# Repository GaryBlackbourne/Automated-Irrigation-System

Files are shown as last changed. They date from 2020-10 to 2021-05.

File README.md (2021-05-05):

# Automated-Irrigation-System

This project is the successor of the watering-system project, which is to be discontinued.

The first prototype of the node unit is released, and ready to be used.

## Current state:
  - Hardware documentation completed
  - Board schematic and layout are in final state
  - board is ready (one prototype finished and tested)

  - node unit source code is ready, and tested
  - manual requests can be made by <node_ip>/measure

## Usage:
  - clone the project
  - install esp-idf framework, and create a project (details in doc/dev-diary.md)
  - insert source files into `main` directory
  - change the SSID and passphrase in `credentials.h`
  - build and flash the project

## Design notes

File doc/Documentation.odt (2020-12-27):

Automated Irrigation System Documentation

Head unit board v 0.1

The Automated Irrigation system is a fully automated modular system for smart home gardening. A central control unit controls multiple head units, that measure the plants condition, and based on the instructions given by the main control, irrigate the plant as needed.

This documentation contains information ONLY abut the alpha version of the head units board.

Board Features:

1. Measure soil moisture
2. Measure temperature
3. Measure light
4. Drive Irrigation pump

Realization:

- Moisture: 555 timer RC capacity measure
- Temperature: in box measurement
- Light: in box measurement
- Watering pump: common source motor drive circuit

Controller: EFM32GG Giant Gecko Starter Kit

PCB editor: KiCAD

Basic Head unit functionality:

The microcontroller drives the sensors, reads temperature, moisture and light data. Based on measured data, the controller drives an external pump, to irrigate the plants’ soil. The connection between the controller and the board is estabilished through the pin array.

Temperature sensor:

The used IC for temperature measurement is an LM75C. The chip uses I2C bus to communicate with the controller, therefore connected to the on board I2C bus. (This bus is shared with VEML7700)

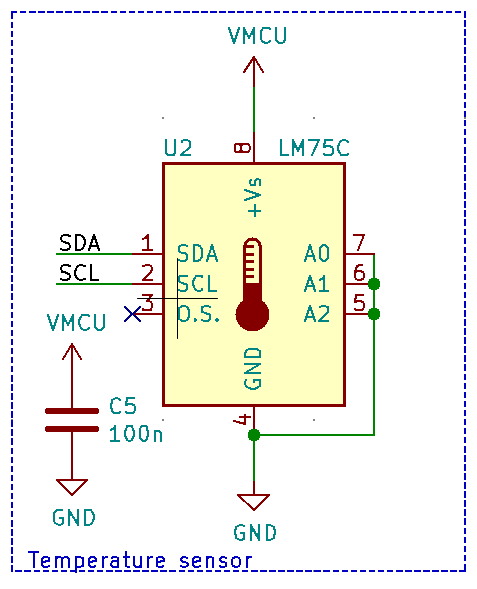
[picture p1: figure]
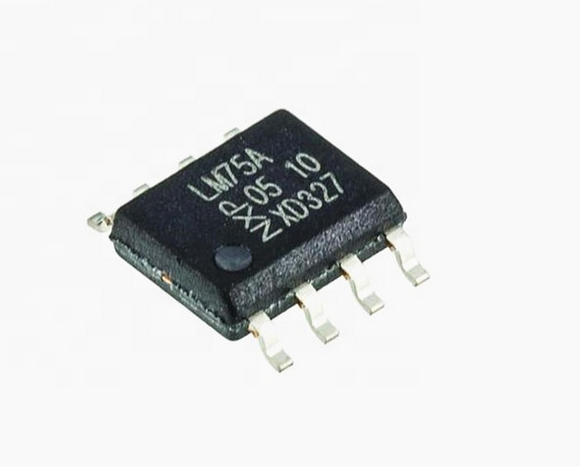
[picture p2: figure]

Moisture sensor:

Moisture measurement method is based on capacity measurement. The measurement is based on a TLC555 timer IC in astable mode. The measured capacity controls the frequency of the timer, which is connected to the PD0 pin on the microcontroller. This pin can be configured as an external clock for pulse counter unit. This method is easier to implement in software, because the capacity measurement becomes a single counting problem.

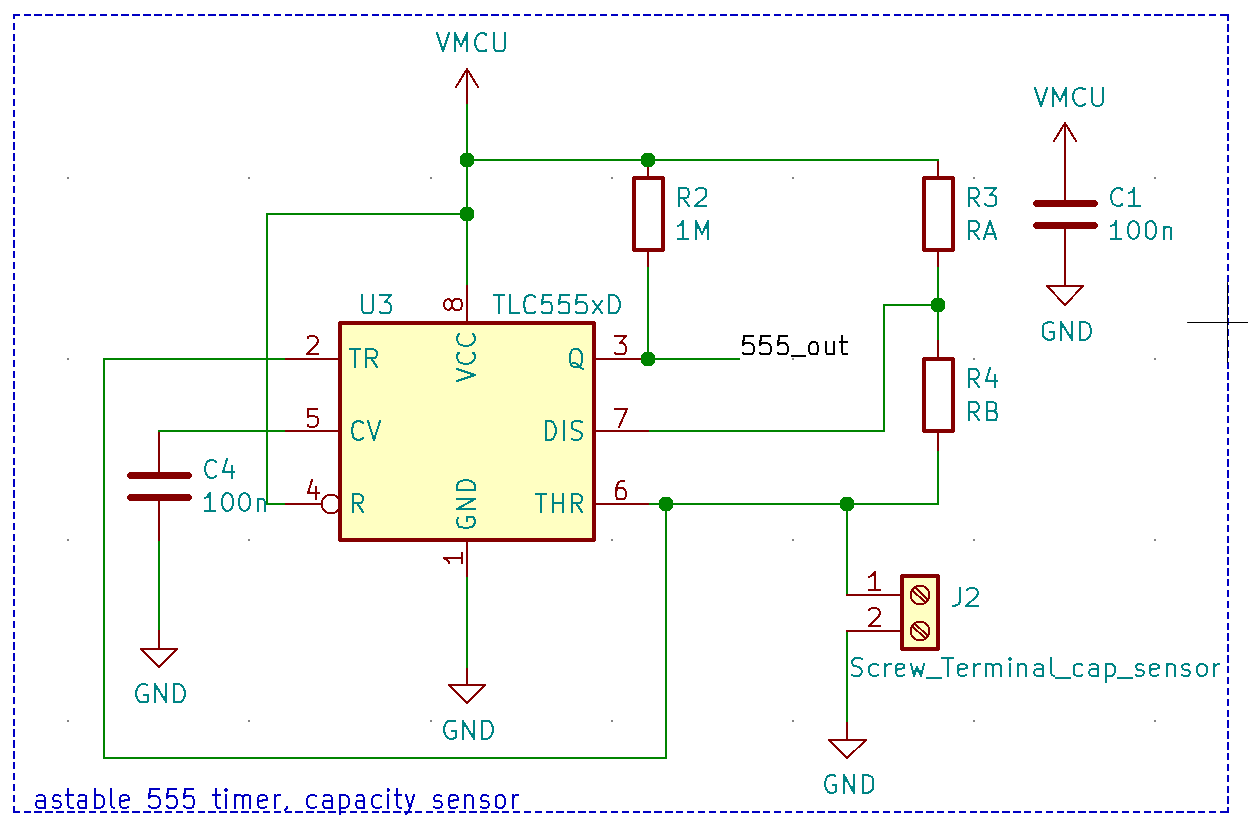
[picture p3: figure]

RA and RB are to be measured with the probe capacity in mind.

Light sensor:

Light measurement is done via VEML7700 IC. This chip is communicating with the microcontroller on I2C protocol, therefore connected to the I2C bus on the board. This component is easy to connect, because the power voltage is 3.3V, no conversion needed. The bus is shared with the temperature sensor.

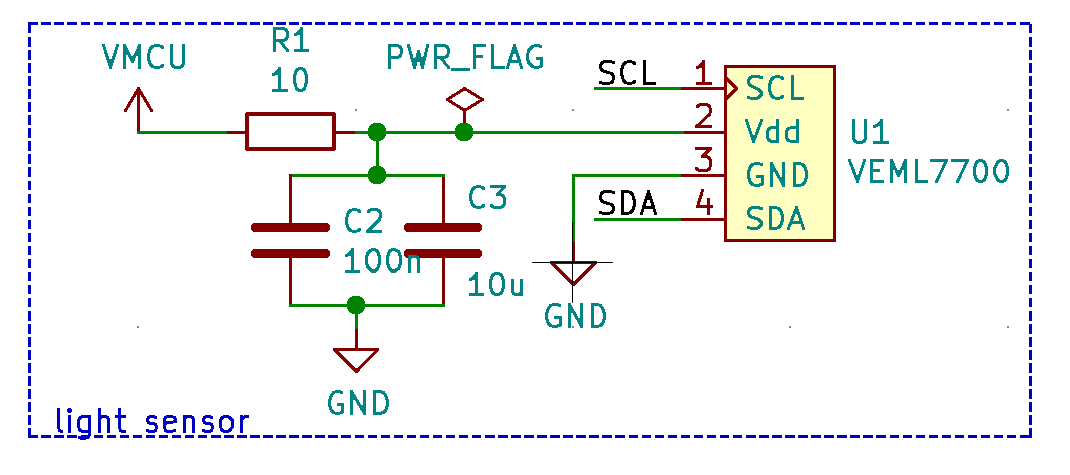
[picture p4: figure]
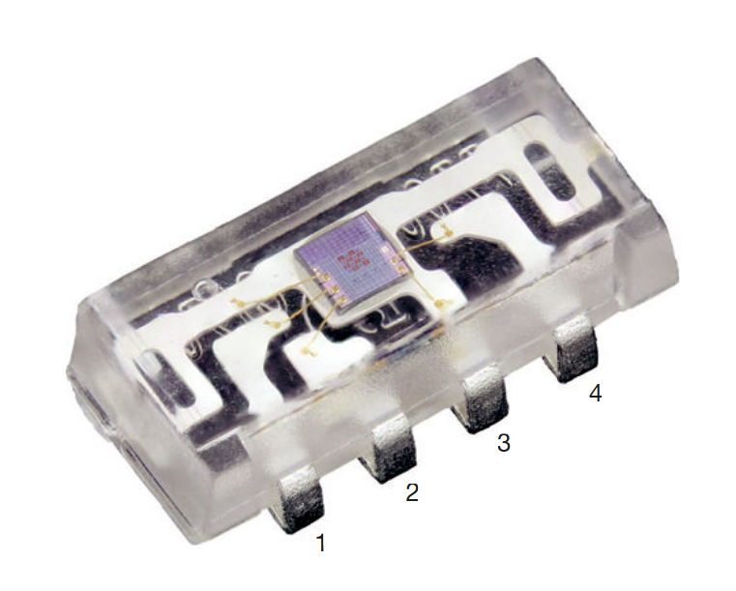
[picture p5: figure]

Package:

Project is packaged in an IP67 plastic case. The case has to protect the device from water, and dust, that may be common at the area of application and may damage the unprotected board. Without casing, only indoor use is possible.

-Pump:

The control element of the system is one 12V pump, a Barwig 0333. The pump requires a 12V power supply that must be connected to the board externally. To maintain the water stream, this pump needs 1.5A–2A current, which makes it necessary to drive with a transistor. The chosen IRLML2502 transistor is a logic level FET. The gate can be driven with a GPIO, and the Drain-Source current allows the required current for the motor.

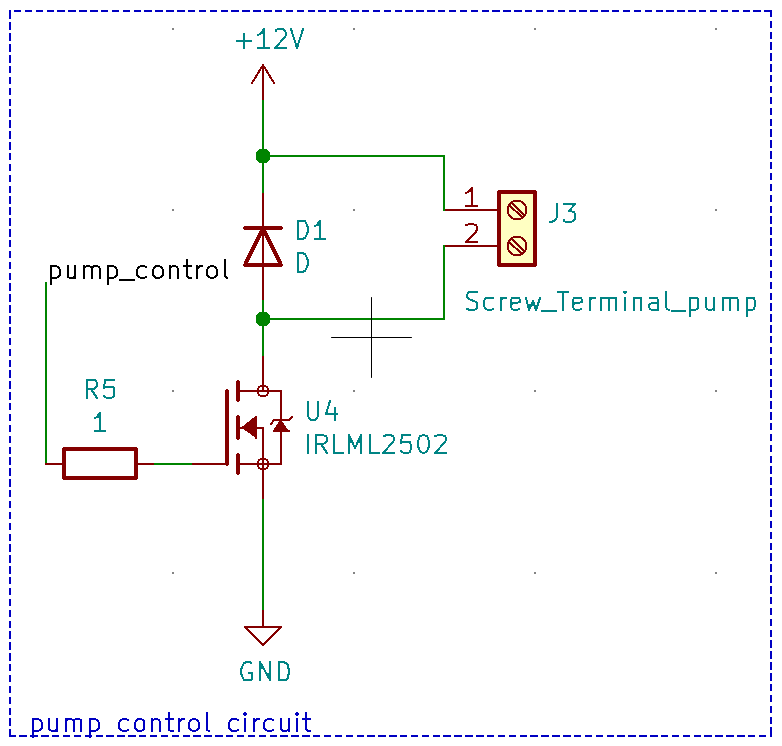
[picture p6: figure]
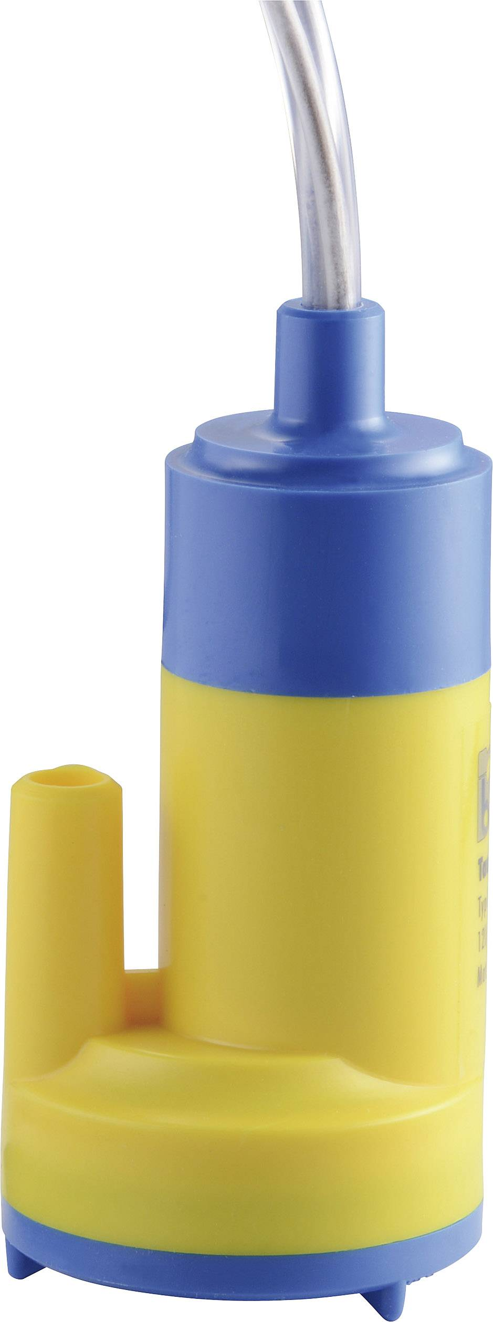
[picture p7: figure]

The pump is driven by a simple common source circuit.

-Power Supply:

The device is powered with an LPV-35-12 power supply unit, which provides 12V DC for the pump.

Alternatively, a barrel jack input is supported if 12V DC input is available. When the barrel jack is in use the LPV power supply is out of use.

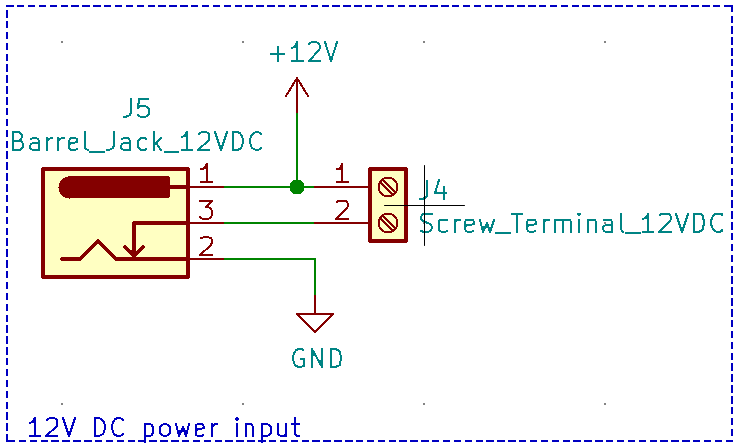
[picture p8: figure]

-Connectors:

The board has five connectors.

1. Pin array to connect to the giant gecko controller. (2x10 pin array female)
2. screw terminal for capacity measure device
3. screw terminal for pump drive
4. screw terminal for 12V DC input
5. barrel jack, for 12V DC input

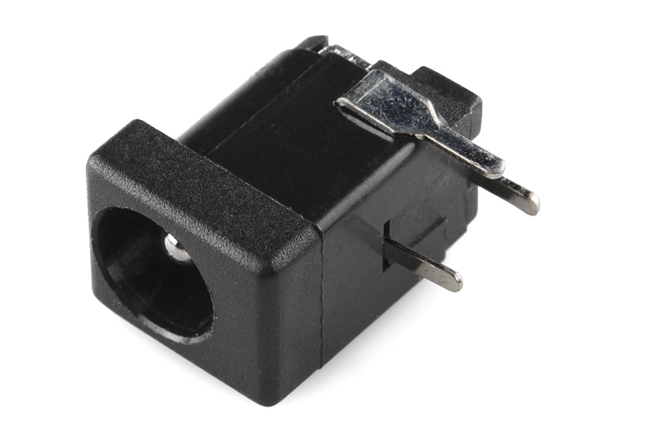
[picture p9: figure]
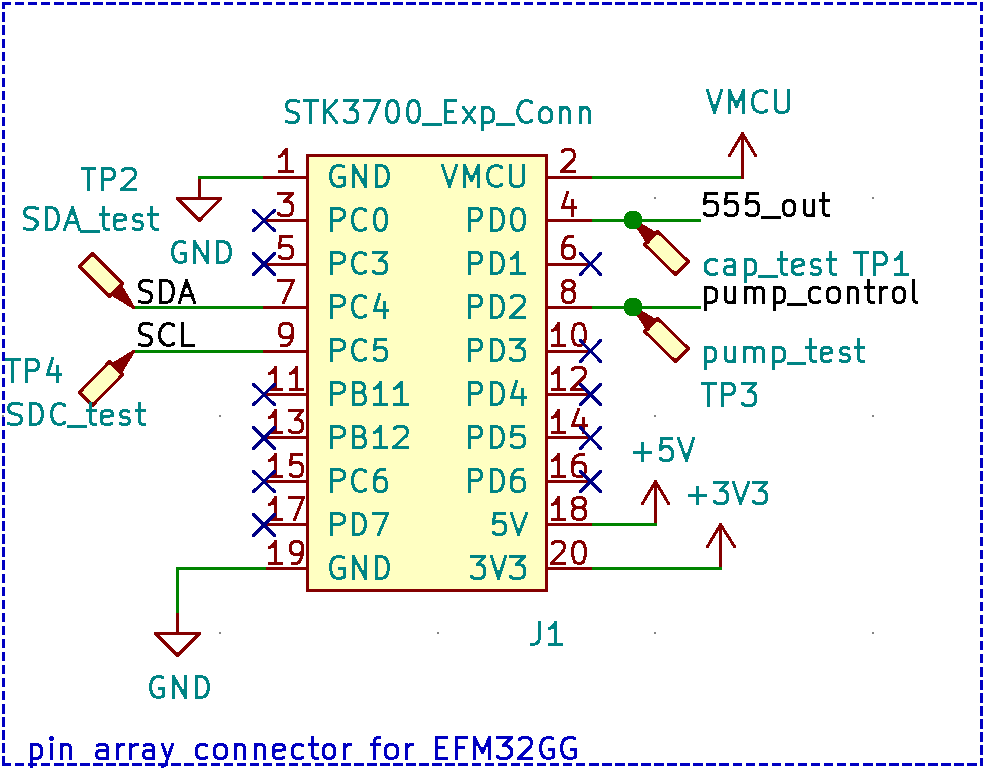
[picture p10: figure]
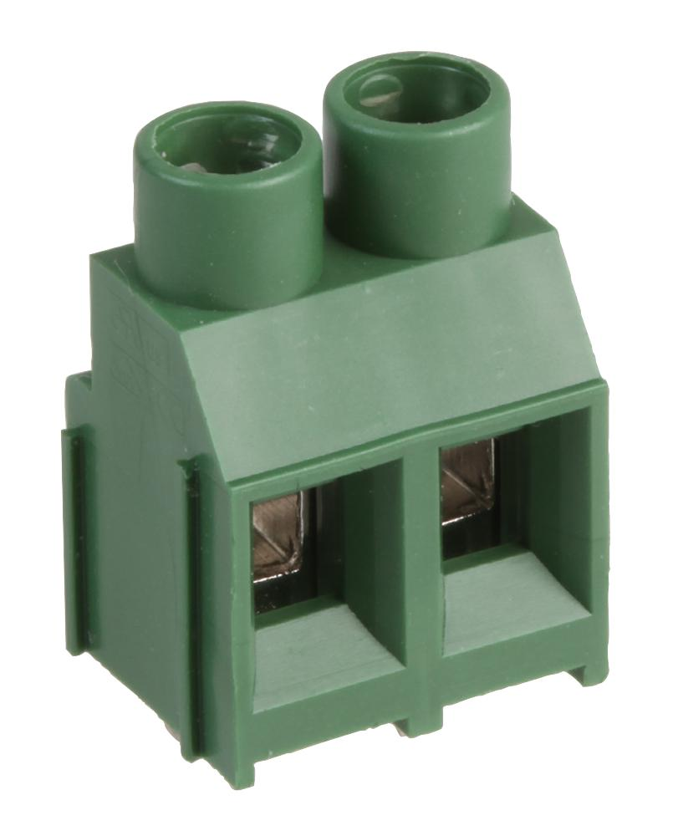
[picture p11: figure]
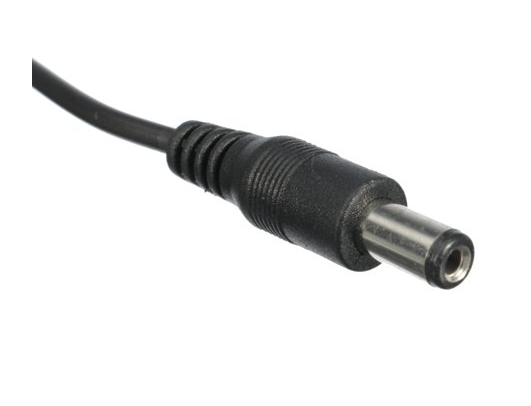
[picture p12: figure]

-Schematic:

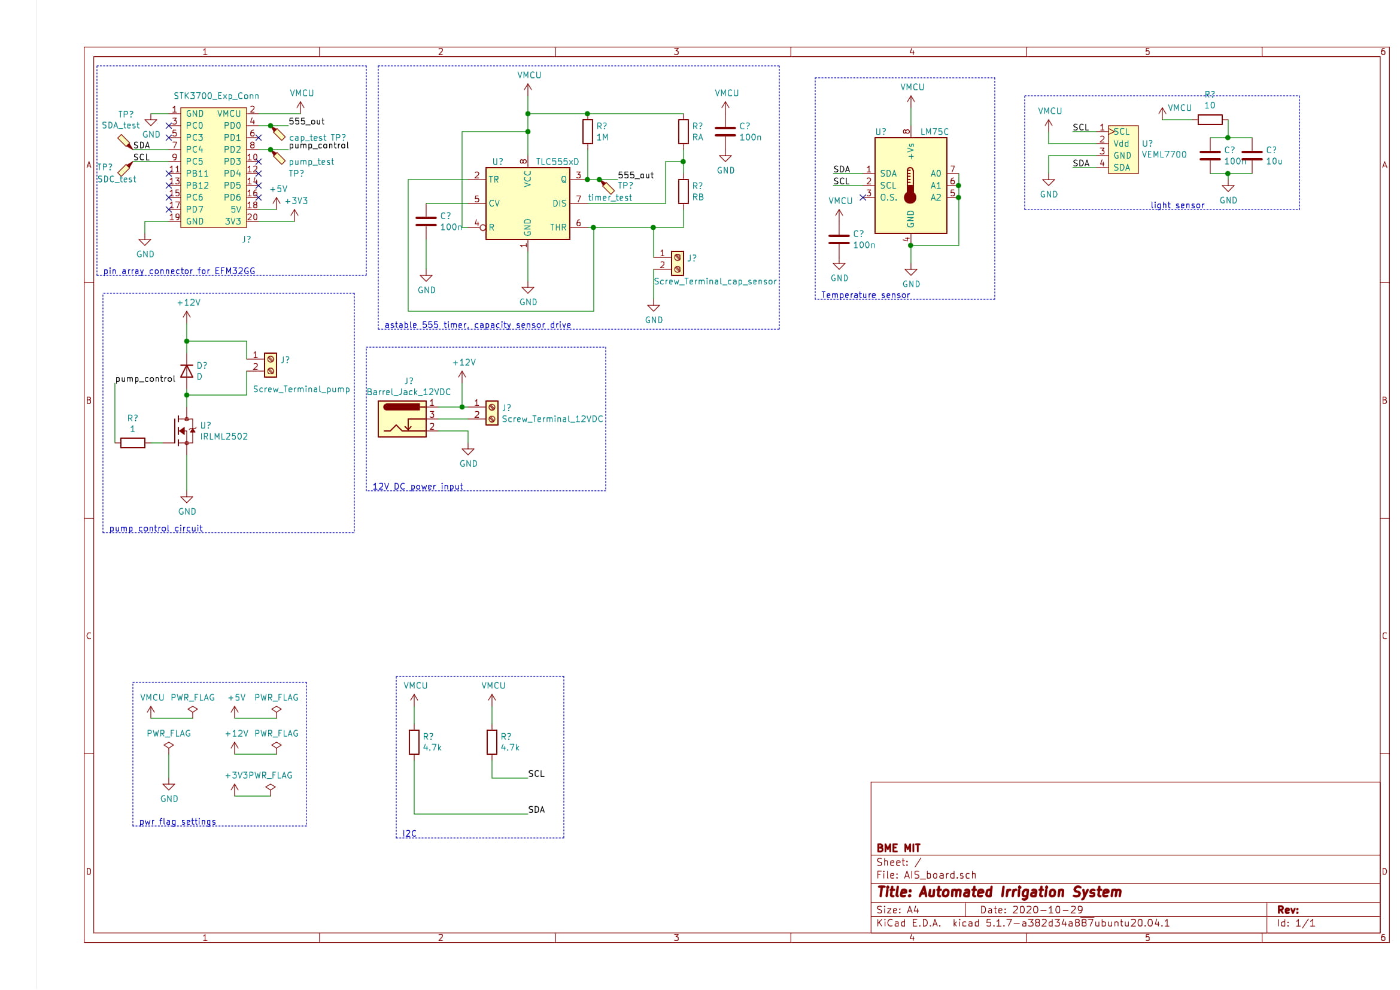
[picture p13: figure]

-PCB layout:

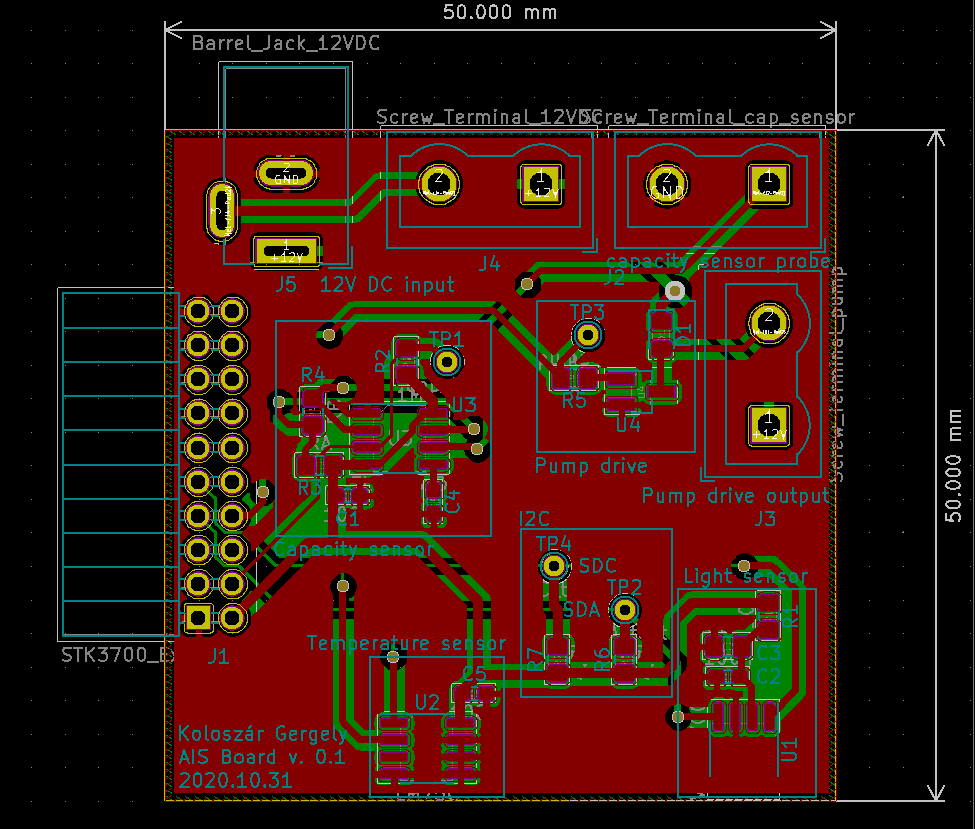
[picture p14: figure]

-Prototype Hardware (kiCAD 3D model):

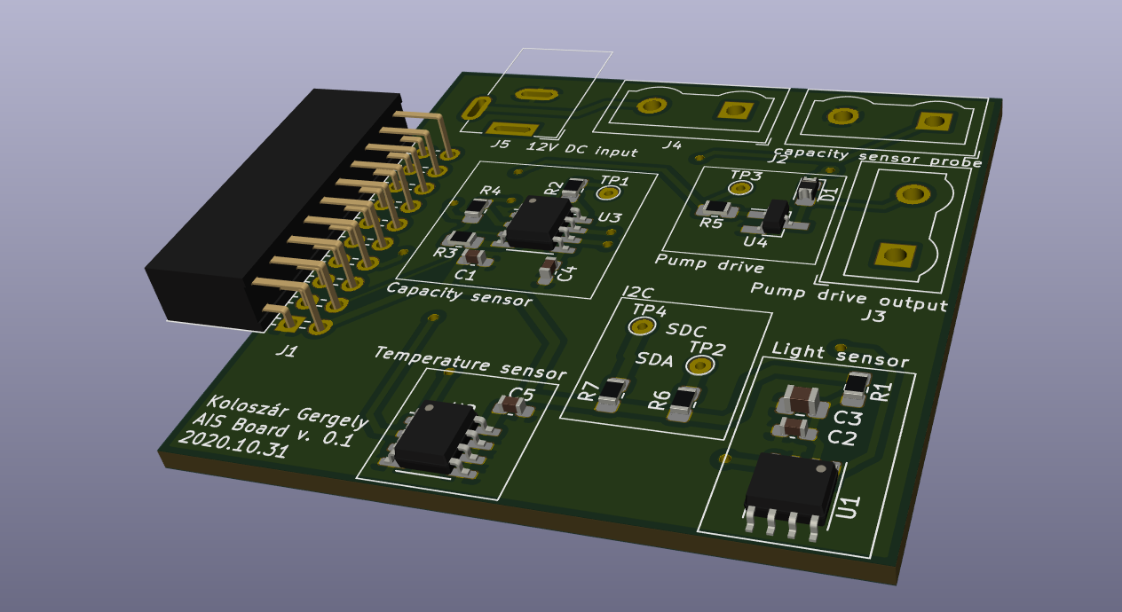
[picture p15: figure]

-Sources:

- the idea of a capacity measurement based moisture sensor (and a different approach):
  - https://theiotprojects.com/capacitive-soil-moisture-sensor-with-oled-display-arduino/
- 555 timer basics:
  - https://www.electronics-tutorials.ws/waveforms/555_oscillator.html
- I2C bus:
  - témalabor classes
- kiCAD:
  - témalabor classes
  - https://www.youtube.com/watch?v=vaCVh2SAZY4
- datasheets:
  - 555 timer: https://www.ti.com/lit/ds/symlink/tlc555.pdf?ts=1609053776577
  - veml7700: https://www.vishay.com/docs/84323/designingveml7700.pdf
  - LM-75: https://www.ti.com/lit/ds/symlink/lm75b.pdf?ts=1609074610236
  - IRLML2502: https://www.hestore.hu/prod_getfile.php?id=6941
  - Barwing 0333: https://asset.conrad.com/media10/add/160267/c1/-/hu/000539082ML04/hasznalati-utmutato-539082-kisfeszueltsegu-buvarszivattyu-12-vdc-12-lperc-6-m-barwig-0333.pdf

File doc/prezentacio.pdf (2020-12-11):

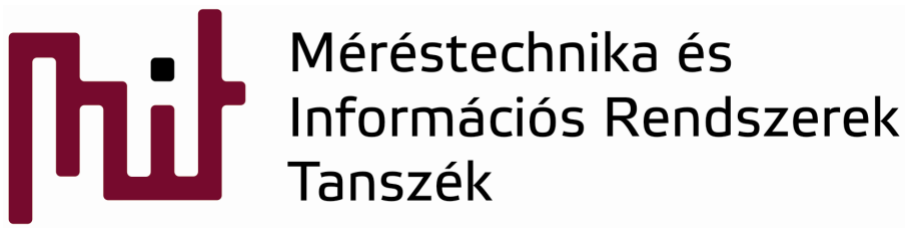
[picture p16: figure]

© BME-MIT 2020 Budapesti Műszaki és Gazdaságtudományi Egyetem Méréstechnika és Információs Rendszerek Tanszék

BSc Témalaboratórium beszámoló

### Öntöző rendszer szobanövényeknek

Szerző: Koloszár Gergely
Konzulens: Kovácsházy Tamás

© BME-MIT 2020 | 2. fólia
- Feledékenység
- Naponta ismétlődő monoton rutin
- Mérhető jelenségek alapján egyszerű döntés
- ->AUTOMATIZÁLÁS

### Motiváció:

© BME-MIT 2020 | 3. fólia
- Legyen egy rendszer
ami automatikusan
foglalkozik velük

●

Így mi elmehetünk
otthonrol, távolrol is
kaphatunk
információkat stb

●

Igények:
– Autonóm működés
– Saját beavatkozási
lehetőség
– Mérési adatok
eltárolása áttekintés
céljából
– Smart Home jellegű
kialakítás, esetleges
integráció

### Specifikáció:

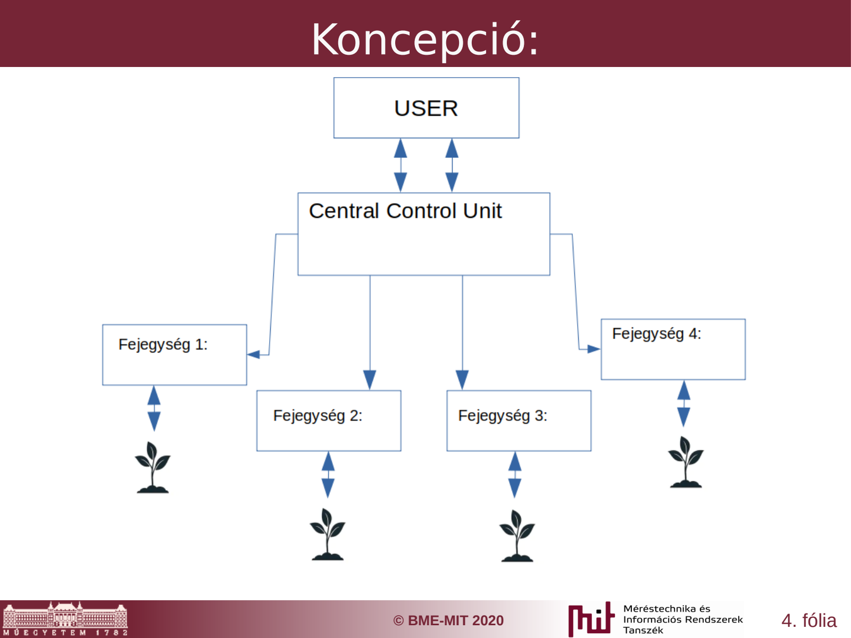
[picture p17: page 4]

© BME-MIT 2020 | 4. fólia

### Koncepció:

© BME-MIT 2020 | 5. fólia

A témalabor feladat ennek a rendszernek a beavatkozó szervét valósítja meg:
– Az elkészített hardware prototípus egy STK3700 mikrokontrollerhez illesztett verzió – A beavatkozó feladata egy adott növény körülményeinek a mérése, és öntözése

### Témalabor:

© BME-MIT 2020 | 6. fólia
- Mérés:
– Fény: VEML7700
– Hőmérséklet: LM75
– Talaj nedvességtartalma: 555 timer + kapacitív mérőfej
- Beavatkozás:
– Öntöző pumpa meghajtása: 12V búvárszivattyú

### A board feladatai:

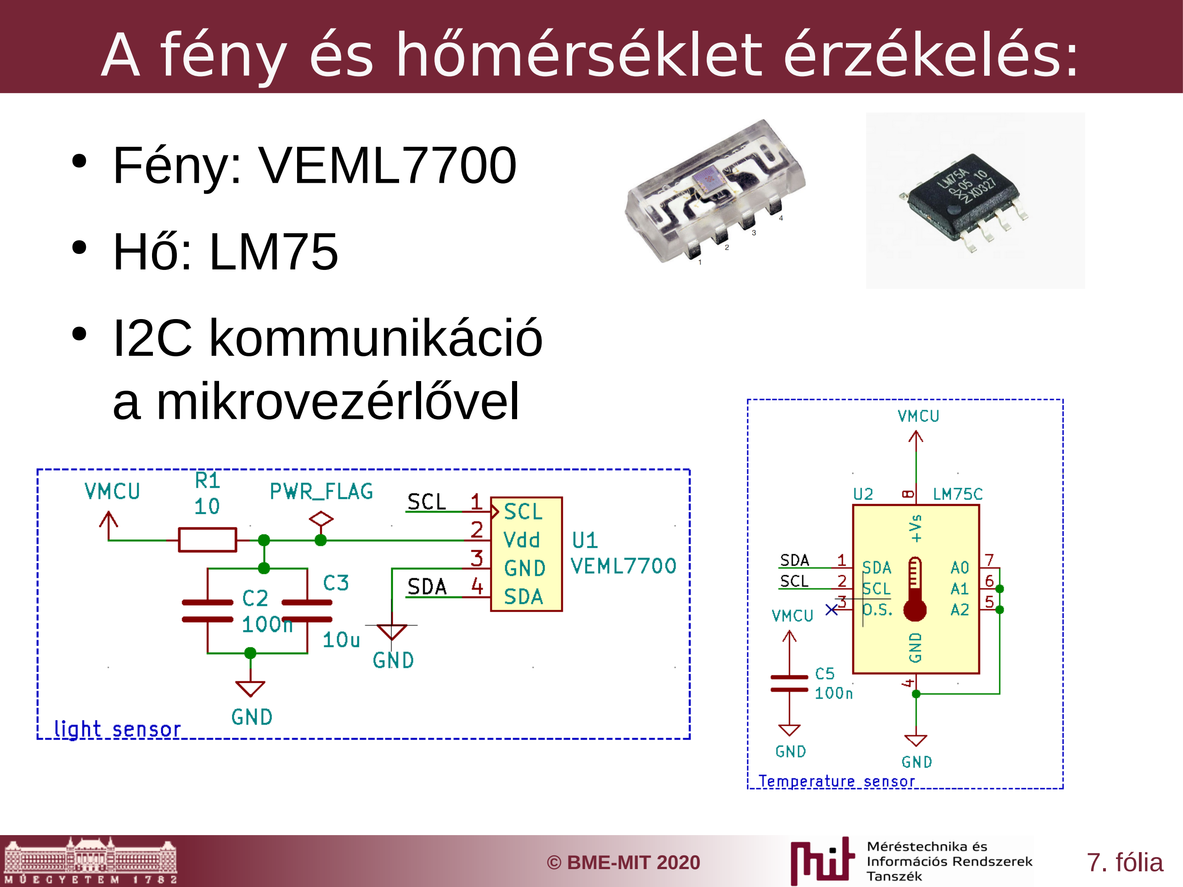
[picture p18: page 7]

© BME-MIT 2020 | 7. fólia
- Fény: VEML7700
- Hő: LM75

●

I2C kommunikáció
a mikrovezérlővel

### A fény és hőmérséklet érzékelés:

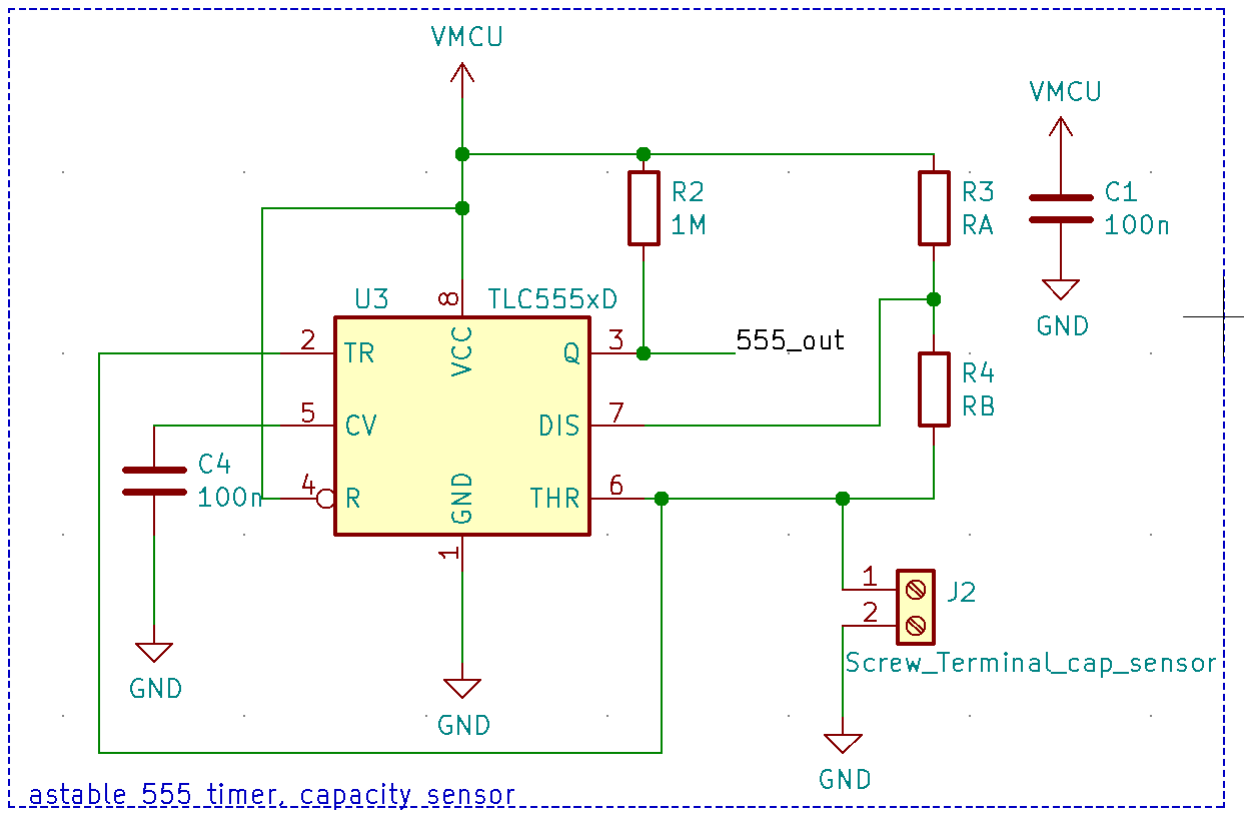
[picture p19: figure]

© BME-MIT 2020 | 8. fólia
- Felhasznált hardware
– 555 timer ic
– Mérőfej: érpár
- A timert astabil módban
használva töltjük fel a
mérőfejet.
- A feltöltés idejét mérve megállapítható a kapacitás a mérőfej két ere között
- A kontrollernek ez egyszerű számlálási feladat

### A talajnedvesség érzékelés:

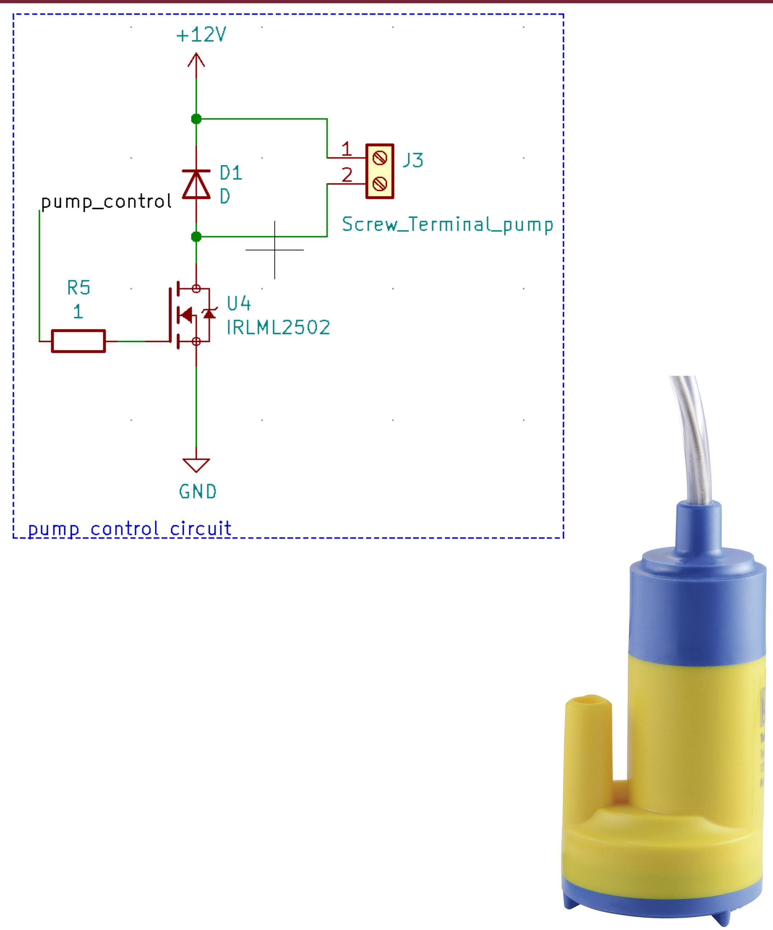
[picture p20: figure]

© BME-MIT 2020 | 9. fólia
- A pumpa 12V
feszültséget
igényel, ezt külső
táp biztosítja
- meghajtásához
egyszerű common
source kapcsolást
használtam

### A beavatkozás:

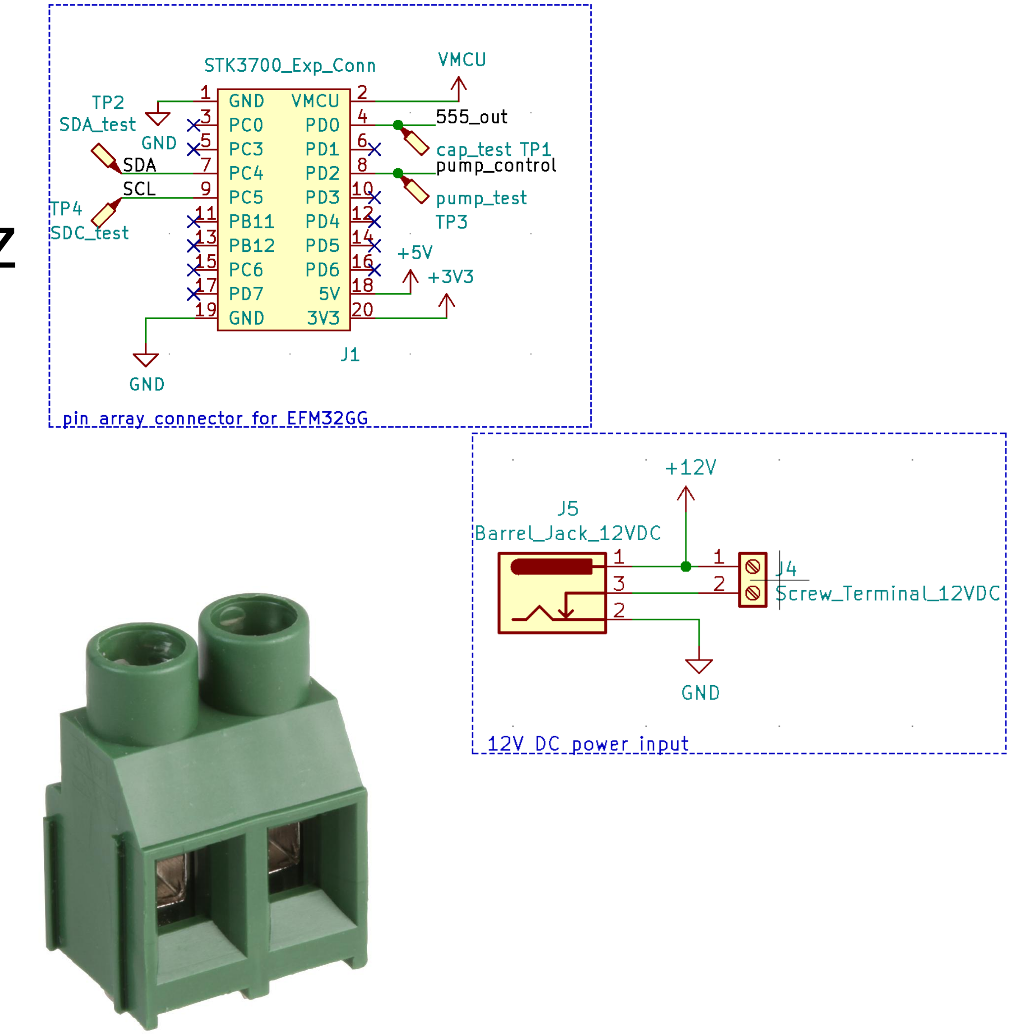
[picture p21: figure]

© BME-MIT 2020 | 10. fólia
- Tüskesor az
STK3700-al való
kommunikációhoz
- 12V táp bemenet
- Pumpa vezérlés
kimenete
- Kapacitásmérő
kimenete
(bemenete)

### A board egyéb elemei:

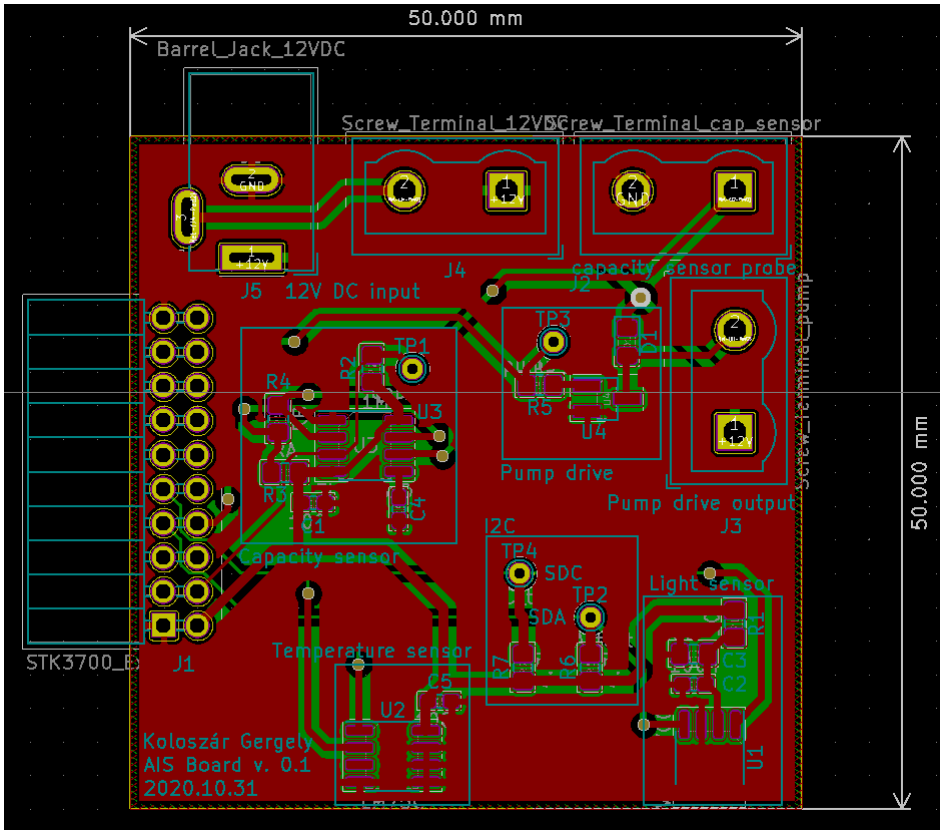
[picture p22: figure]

© BME-MIT 2020 | 11. fólia

### Az elkészült PCB terv:

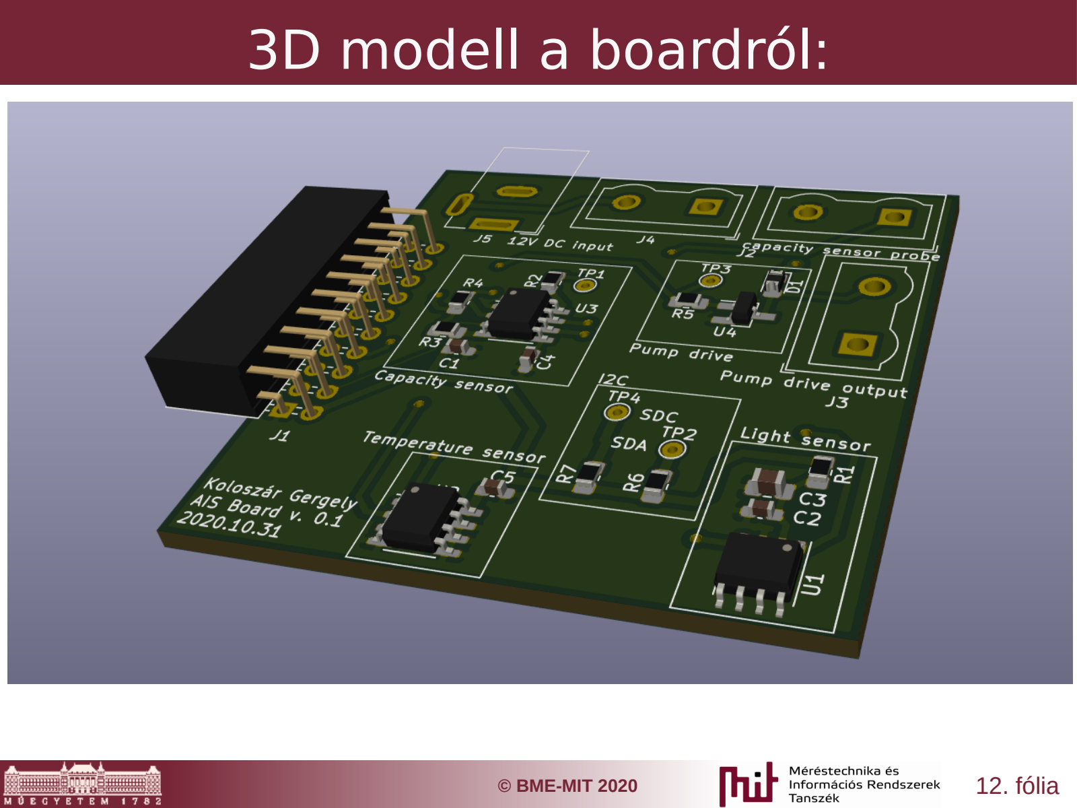
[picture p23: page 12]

© BME-MIT 2020 | 12. fólia

### 3D modell a boardról:

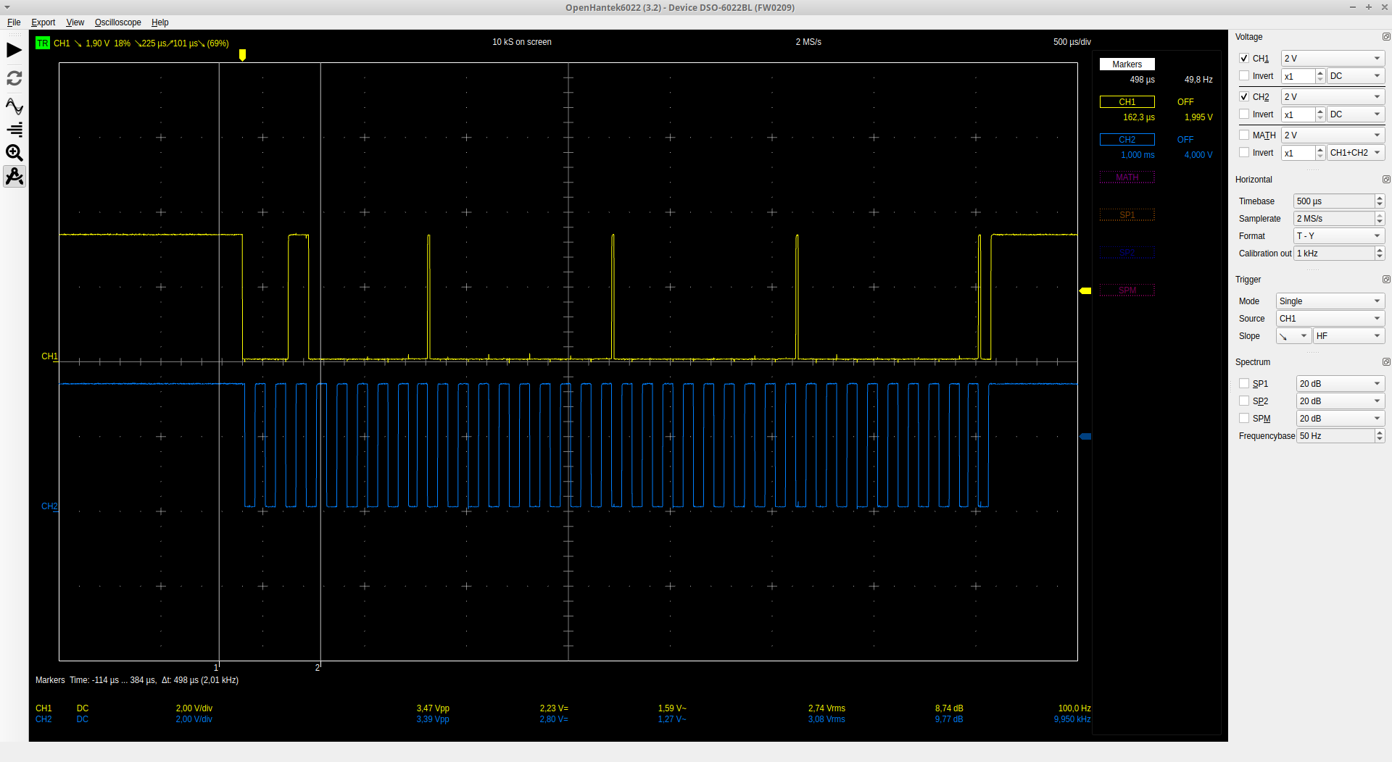
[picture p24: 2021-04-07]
doc/.pic/I2C_VEML_INIT_SIG.png

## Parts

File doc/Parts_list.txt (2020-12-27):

Board - schematic in repository

EFM32GG Giant Gecko starter kit

TLC555CD SMD - (moisture sensor timer)
	https://www.hestore.hu/prod_10029037.html 
	100.290.37
LM75C - (temperature)
	https://www.hestore.hu/prod_10025446.html
	100.254.46
VEML7700 - (ligt)
	https://hu.farnell.com/vishay/veml7700-tt/ambient-light-sensor-i2c-3-6v/dp/2627812
	2627812
IRLML 2502 - (transistor)
		
	100.328.50
1N4148-0805 - (diode)
	https://www.hestore.hu/prod_10000050.html
	100.000.50
LPV-35-12 - (pwr supply) [témalaborbol kimarad]
	https://lomex.hu/pdf/(mw)_lpv-35-spec.pdf
	
Barwig 0333 - (pump) [témalaborbol kimarad]
	https://www.conrad.hu/hu/kisfeszueltsegu-buvarszivattyu-12-vdc-12-lperc-6-m-barwig-0333-539082.html

MC000052 - (screw terminal) x 3
	https://hu.farnell.com/multicomp/mc000052/terminal-block-wire-to-brd-2pos/dp/2008023
	
SMD:
	R:
		4.7k x 2
		1    x 1
		1M   x 1
		10   x 1

	RA, RB -> to be optimised
	
	C:
		100n x 4
		10u  x 1

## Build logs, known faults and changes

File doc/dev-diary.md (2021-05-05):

# AIS Project development diary

## 18/03/21:

### Initial state:
The projects initial state is inherited from "temalab" project, where from we have the board with the following properties:

- connectivity with stk3700 uController dev board (EFM32GG)
- I2C bus
  - Light sensor (VEML7700)
  - temperature sensor (LM-75)
- pump drive circuit
- device for capacity measurement (555 timer)
- 12VDC input
- screw terminals
  - capacity probe
  - pump

the board is manufactured, and measured, results:

- all I2C peripherals working
- timer working with strange duty cycle
- pump drive untested as of yet

### Goal:

The final goal is to make a system which can be set up in a domestic environment. The system consists of two main parts:
- node modules, which are to communicate with the core unit, receiving instructions, and watering plants. The applied controller is an ESP32.

- Core module, which is most likely a raspberry pi taking care of any type of user input, and controlling the nodes.

### Progression:

Several projects have been created using simplicity studio. The main goal is to test all devices using this prototype board, and the stk3700 and test all functionalities.

The last couple days I was struggling with PCNT configuration and timer configuration.
I2C configuration was done through the simplicity studios built in configurator. With some help, I was able to get I2C working.

Pulse counter is however unresponsive in the main project. I decided to launch a sample project where everything is configured properly. The results was good, the peripheral was working as intended.

I have built an external square signal generator from an ESP32 for testing purposes, using arduino framework, with platformIO. (This framework is easy to use, and platformIO is an easy to use, comfortable tool) This small 'module' is generating a low frequency square signal, and makes it easier to setup a new peripheral.

I started to change the code in the sample project, and comment out anything that is not strictly required for my application. This way the project is still functioning, compilation was successful.  In debug mode i tracked the counter value in a variable, the peripheral was working.

This makes me think that something was not properly configured with the original project.

Simplicity Studio 5s new project structure is much more chaotic for this type of small projects. I was thinking about creating a raw project where all unnecessary stuff is removed. Basic configuration, and learning could be much efficient that way.

## 19/03/21

### Hardware bugfixes:

An issue has been found in the 555 timer-based capacity sensor. The RA and RB resistors were soldered in a wrong order, which caused extremely high duty-cycle while measured. After the exchange, the board is fully functional, perfect 50% duty-cycle was measured with oscilloscope, frequency was shifted when the capacity connected to the board changed. There is no hardware malfunction discovered yet, the external power-, and drive systems are to be tested.

### Change in prototype:

No explanations were found concerning the Pulse Counter malfunction, in order to speed up the development process, this bug is no longer on todo list. I have a working example with stk3700, and planned to develop one with ESP.

### New Controler:

Experiments started with ESP32 development. Used development tools:
- espressif framework
- vs code
- platformIO plugin

Arduino framework was planned to be used, but with arduino, there seem to be no way to use the PCNT module of the chip.
Further research needs to be done about the characteristics of this module (especially frequency).

The ESP32 uses freeRTOS system, which is preinstalled. This might come handy when I develop networking while reading different sensor values. Although learning freeRTOS system is now a prioritized task.

### New platform:

Espressif controllers can be developed with Arduino IDE, there own IDE, or platformIO. The choice for this project is platformIO, because of the comfortable code completion, function tracking and compatibility with both frameworks (Arduino / Espressif-SDK).

Minor problems occurred during the first compile, after getting used to the environment problems were solved.
A basic project was created, testing GPIO-s with a 'blink' functionality.

## 03/04/21

For easier development I have installed a pure ESP-IDF. Removed platformIO, I try to work with only the framework, and compile my code via terminal. Installation was tough, fish script doesnt seem to work, I needed to use bash. This should be taken care of in the near future to remove a large handicap.
The problem lies with environment variables, I'll write down the solution, as soon as I find them.

### Tutorials were followed:
https://www.youtube.com/watch?v=5IuZ-E8Tmhg
https://docs.espressif.com/projects/esp-idf/en/latest/esp32/get-started/index.html *note that the fish scripts are failed to work*

### First test:
First test project, a simple blink example was successfully uploaded to the chip. I used VS Code, but mostly integrated terminal. Further research needed, how to embed a terminal like bash or fish, into VS Code, and how to get fish working.

For now, I can create projects manually, and compile them from CLI using ESP-IDFs `idf.py build`, and `idf.py flash -p /dev/ttyUSB0` commands. Debugging is not available for the time being.

Tasks are given:

-find fish-s problem in the scripts
-integrate fish, or bash into VS Code
-create a project, and test GPIO, I2C, and PCNT modules.

## 04/04/21

New morning, new thoughts. I seem to have found a solution for the problem. It seems the init script of fish does not work as intended. I set bash as the embedded terminal for VS Code, and created an alias in `.bash_aliases`, for initializing the shell for code compiling.

The alias:
```bash
alias idfinit=". $HOME/<idf-directory>/export.sh"
```

The `export.sh` code was copied from installation manual, and does all the setup work (initializing environment variables for example). The main problem is that bash can not execute any init command, and fish is still not working with the given scripts. By the way, fish has an argument, `-C` which does exactly what we need here.
If I find a way to solve this issue, I change my shell in VS Code.

### New project initialization:
1. Create a directory
2. Save as workspace, then setup the workspace terminal with the following JSON:

``` JSON
{
"folders": [
  {
    "path": "."
  }
],
  "settings": {

    "terminal.integrated.shell.linux": "/usr/bin/bash",
    "terminal.integrated.shellArgs.linux": [
    ]
  }
}
```
(The JSON is the created workspace file : `<project-name>.code-workspace`).

These settings are to set bash as default shell. (this move might be temporary due to bash / fish support difference mentioned above)
3. After saving workspace, allow it to modify embedded shell
4. Open the terminal, and write `idfinit` to initialize shell for development
5. Setup project, using `idf.py create-project`
  - `--help` is useful argument to find out how to do that
  - `idf.py create-project <project-name> -p . ` will create a new project directory in current folder, and initialize project. The output should be:

  ```
  Executing action: create-project
  The project was created in <project-directory>

  ```
  - this instruction creates a `CMakeLists.txt`, a `main` directory, `CMakeLists.txt` inside this directory, and `<project-name>.c` file, in my case `esp_gpio_test.c`.

6. For the following steps to work, build the yet empty project with `idf.py build` command in the terminal, this creates `.vscode` and `c_cpp_properties.json`.
7. To make includes work, we have to set the includePath setting
  - there should be a driectory called `.vscode` next to the project directory, and there is a file called `c_cpp_properties.json` in it.
  - in this file we can append the `includePath` section if needed
  - `/home/<username>/dev/esp-idf/**` line adds the IDF directory
  - now includes should work (and ctr + LMB helps to track)
8. To build, the working directory should be the one containing, the main source file
9. Build is done via `idf.py build` command
10. Flash is done via `idf.py -p /dev/ttyUSB0 flash` commands

### First handmade project

Using the method described above, I have created a simple task, which initialized a simple GPIO port, and sets it to high level.

No errors occurred.

## 05/04/21

### Problems with VS Code includes.
I have encountered a minor error in VS Code. A specific file, called sys/reent.h cannot be opened. Compiler doesn't seems to care much about it, only the editor.

Found a solution:

I inserted the following two lines into c_cpp_properties.json:
``` JSON

"compilerPath": "${config:idf.toolsPath}/tools/xtensa-esp32-elf/esp-2020r3-8.4.0/xtensa-esp32-elf/bin/xtensa-esp32-elf-gcc",
"compileCommands": "${workspaceFolder}/<your-project-directory>/build/compile_commands.json",

```

Now no errors shown. I have no clue what these lines done. Probably fixed some path issues.

source:
https://www.esp32.com/viewtopic.php?f=13&t=16585

### Serial communication

Found an easy way with `ESP_LOGI()`. This is a define of some sort, but available to send minimal data through serial port, which can be monitored with `idf.py monitor`.
This might be useful when debugging low level peripherals.

Watchdog has been turned off, for development purposes. It can be done by executing `idf.py menuconfig` command, then select Component config -> ESP System Settings, in which the `Interrupt watchdog` and `Initialize Task Watchdog Timer on startup` options can be disabled.

### I2C project:

I have initialized a new project to test I2C behavior in ESP32. For the time being, I will concentrate on the master side of the communication. The main sequence of the I2C usage is this:

  - create initialization struct (`i2c_config_t`)
  - set mode, SDA-SCL signal pins, and pullups
  - in case of a master device, we can set the clk speed as well
  - we need to call two functions:
    - `i2c_param_config()` where you select the device (called i2c port)
    - `i2c_driver_install()` where you install the driver for the specific device (I am not sure what this does)
  - we set the sequence up by the following:
    - i2c_cmd_handle_t cmd = i2c_cmd_link_create();
      - here we create a handler for the communication
      - this is a `void*` typedef inside, I presume the whole sequence
    - i2c_master_start();
      - adds the start bit at the beginning
    - i2c_master_write_byte();
      - writes an entire byte to the sequence, you can use this to address a device on the bus.
      - in the arguments list we can decide if we want to have an ACK signal at the end
    - i2c_master_read();
      - this one is self-explanatory, reads data from the bus
      - in the arguments we can tell the length of the data, as well as provide a variable to store it
    - i2c_master_stop();
      - puts a stop bit at the end
    - i2c_master_cmd_begin();
      - starts the sequence by sending all queued commands.
      - this function starts the communication, and as long as a command presents, it will continue sending it.
      - we can stop the sequence by calling th next function:
    - i2c_cmd_link_delete();
      - empties queue and stops transmitting

I2C Bus and the device seems working. Some problems occurred at the addressing, the correct way is `(<base address in 8 bit> | I2C_MASTER_READ)` as `i2c_master_read()`s argument.
The LM75 requires at least 300ms to reload measured data into data register, therefore we need at least 300 ms between requests. I have not found a better solution than pack the whole method into one function, and call it in a whiletrue with delays.

At least one peripheral is working with ESP already.

## 07/04/21

I tried to get the I2C working today on the VEML7700 but no success yet. I measured both I2C buses, and got these results, when tried to analyze the signal:

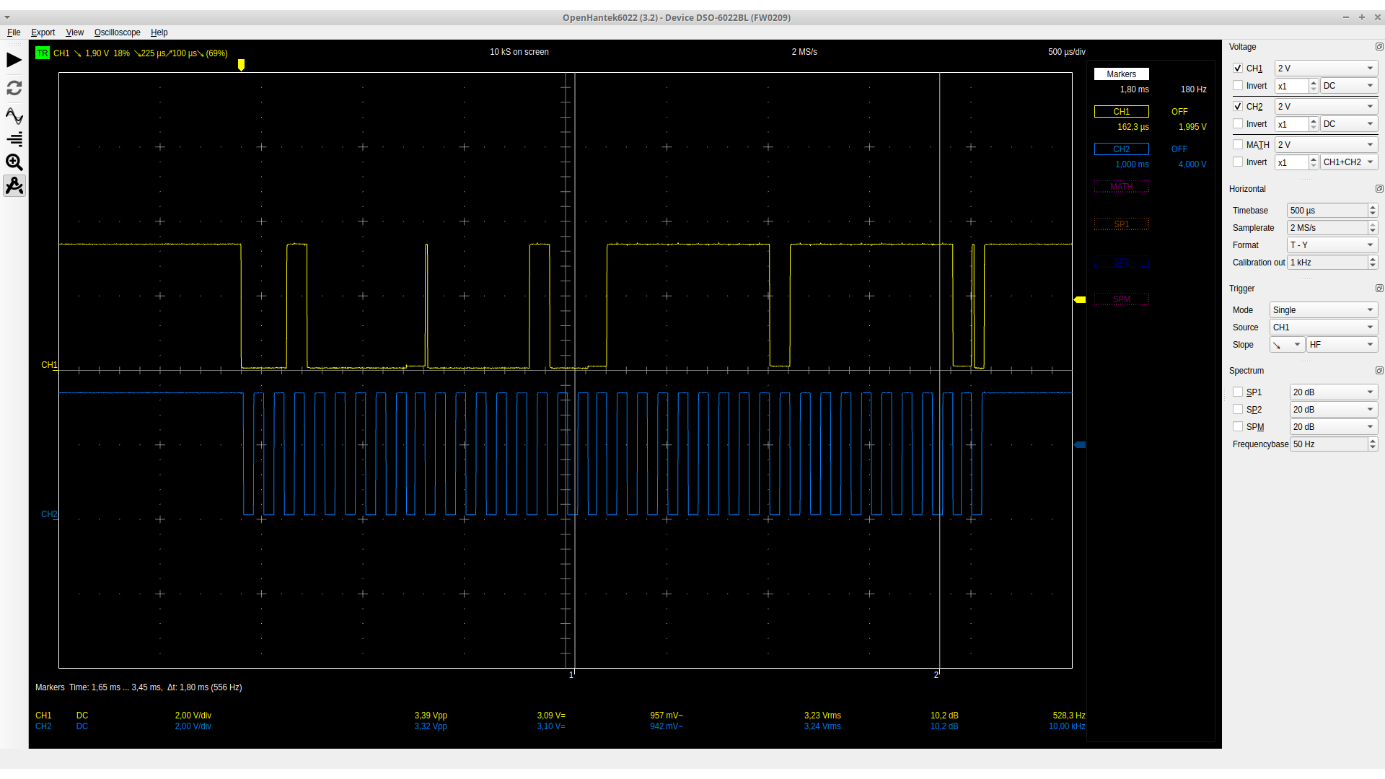
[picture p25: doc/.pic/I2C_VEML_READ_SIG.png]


`0 0 0 1 0 0 0 0 0 0 0 0 0 0 0 1 0 0 0 1 1 1 1 1 1 1 1 0 1 1 1 1 1 1 1 1 0 0 1`

And I decoded it like this:

| start | address | R/W | ACK | command code  | ACK | data 1 | ACK | data 2 | ACK | stop |
| --- | --- |  --- | --- |  --- | --- |  --- | --- |  --- | --- | --- |
| 0 | 001 0000 | 0 | 0 | 0000 0100 | 0 | 1111 1111  | 0 | 1111 1111  | 0 | 1 |

Problem was a missing restart signal. This is still not solved.

Init sequence also got measured:



| start | address | R/W | ACK | Command code | ACK | data 1 | ACK | data 2 | ACK | stop |
| --- | --- |  --- | --- |  --- | --- |  --- | --- |  --- | --- | --- |
| 0 | 001 0000 | 0 | 0 | 0000 0100 | 0 | 0000 0000  | 0 | 0000 0000  | 0 | 1 |

And it seems correct. I am suspicious about the repeated start signal.

Small progress has been made. With the following function, I was able to read the measured light data correctly, at least most of the time.

``` C

void readVEML (uint8_t* data, uint8_t size){

    i2c_cmd_handle_t cmd = i2c_cmd_link_create();

    i2c_master_start(cmd);
    i2c_master_write_byte(cmd, (VEML_ADDR | I2C_MASTER_WRITE), true);
    i2c_master_write_byte(cmd, VEML_COMMAND, true);

    i2c_master_start(cmd);
    i2c_master_write_byte(cmd, (VEML_ADDR | I2C_MASTER_READ), true);
    i2c_master_read(cmd, data, size, I2C_MASTER_ACK);

    i2c_master_stop(cmd);

    i2c_master_cmd_begin(I2C_NUM_0, cmd, 1000 / portTICK_PERIOD_MS);
    i2c_cmd_link_delete(cmd);

    return;
}

```
Sometimes, it just breaks down, no matter what. I also experience huge desynchronisation in the program. I have configured a LED to blink every time when the main loop is executed, and it's a mess.

It seems that the issue was the incorrect define as the last argument of `i2x_master_read`, now it works most of the time.

I have increased the maximum wait ticks from `1000 / portTICK_PERIOD_MS` to `10000 / portTICK_PERIOD_MS`, now the delays seem much larger. It's worth checking out.

Found a way to debug:

``` C
ESP_LOGE(TAG,"Error is: %s", esp_err_to_name(error));
```

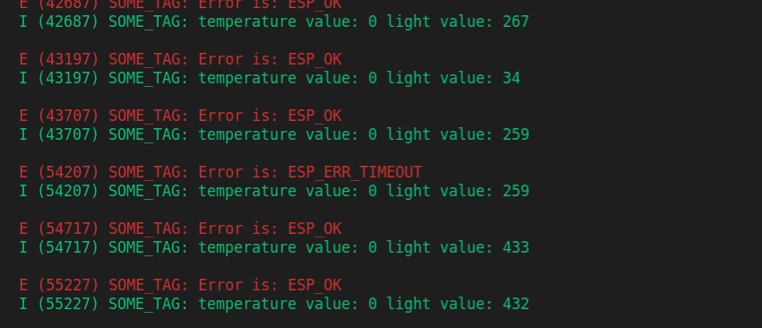
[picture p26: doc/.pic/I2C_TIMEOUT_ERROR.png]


It seems, somehow I managed to create a timeout error. At TIMEOUT the variable doesn't change.

Finally I have made a working read function with the following code:

``` C

void readVEML (uint8_t* data, uint8_t size){

    i2c_cmd_handle_t cmd = i2c_cmd_link_create();

    i2c_master_start(cmd);
    i2c_master_write_byte(cmd, (VEML_ADDR | I2C_MASTER_WRITE), true);
    i2c_master_write_byte(cmd, VEML_COMMAND, true);

    i2c_master_start(cmd);
    i2c_master_write_byte(cmd, (VEML_ADDR | I2C_MASTER_READ), true);
    i2c_master_read(cmd, data, 1, I2C_MASTER_ACK);
    i2c_master_read_byte(cmd, data+1, I2C_MASTER_NACK);

    i2c_master_stop(cmd);

    esp_err_t error2 = i2c_master_cmd_begin(I2C_NUM_0, cmd, 1000 / portTICK_RATE_MS);
    i2c_cmd_link_delete(cmd);

    //ESP_LOGE(TAG,"Error Command %s", esp_err_to_name(error1));
    ESP_LOGE(TAG,"Error : %s", esp_err_to_name(error2));

    return;
}

```

It's working 97% of the time. Random ESP_TIMEOUT, and ESP_FAIL errors still happen, but rarely.

## 08/04/21

Today I looked into the PCNT modules setup function, and struct. It worked at first try!  A surprise to be sure, but a welcome one. The init phase goes like any other, we have an init struct, set our parameters then call an init function, (or config function to be precise).

PCNT init struct contains the following data:

``` C
pcnt_config_t pcntInitStruct = {
        .pulse_gpio_num = GPIO_NUM_22,
        .ctrl_gpio_num = GPIO_NUM_23,
        .lctrl_mode = PCNT_MODE_KEEP,
        .hctrl_mode = PCNT_MODE_KEEP,
        .pos_mode = PCNT_COUNT_INC,
        .neg_mode = PCNT_COUNT_DIS,
        .counter_h_lim = PCNT_LIMIT_MAX,
        .counter_l_lim = 0,
        .unit = PCNT_UNIT_0,
        .channel = PCNT_CHANNEL_0
    };
```
I initialized everything that is defined in the struct with these parameters. Most of them are defines in the `pcnt_types.h` except `PCNT_LIMIT_MAX` which i have defined as 65535 (0xFFFF).

the PCNT module can be controlled easily with the following functions:
- `pcnt_get_counter_value`
- `pcnt_counter_pause`
- `pcnt_counter_resume`
- `pcnt_counter_clear`

They do exactly what their name tells.
Using an unsigned variable might be useful in the future, because there is no point in negative values in our case.

Measurements represent the expected values:

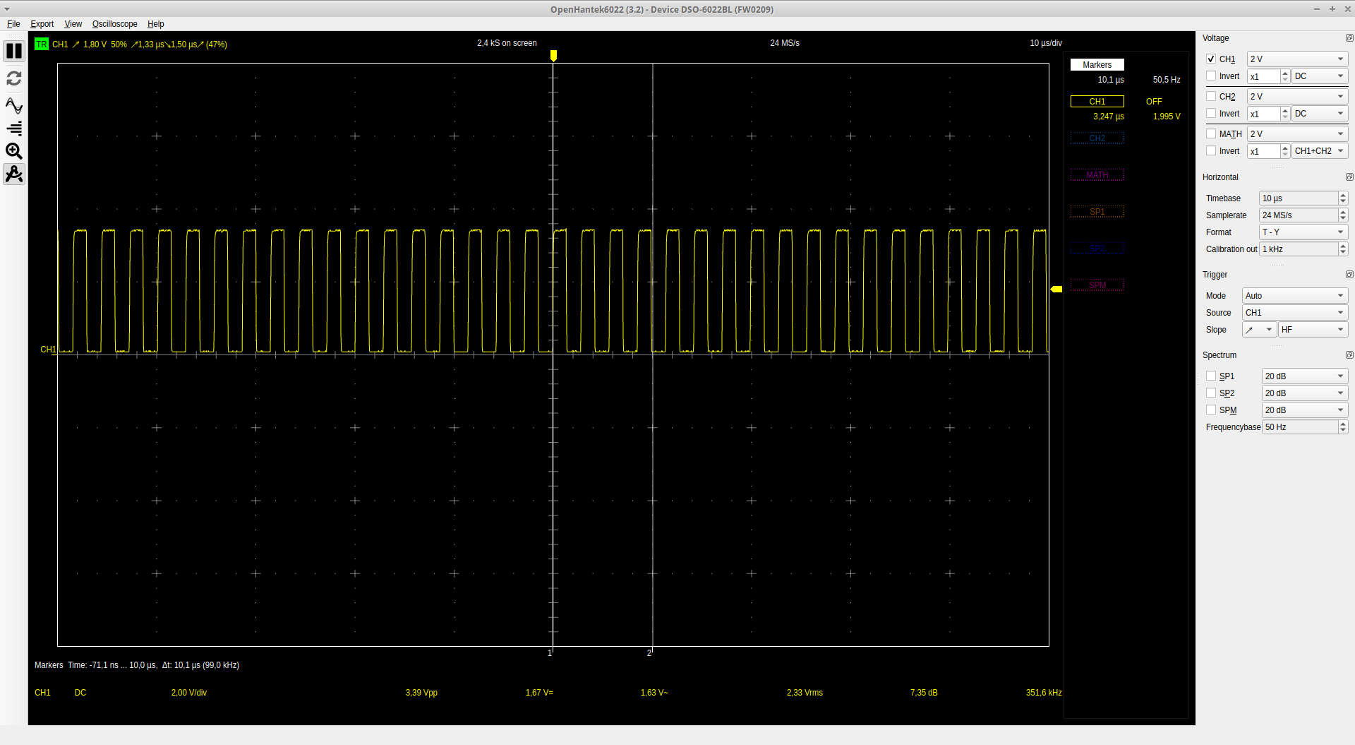
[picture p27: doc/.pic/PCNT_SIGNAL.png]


My signal has 351 kHz frequency which means, it should be around 351-2 pulses in one millisecond.

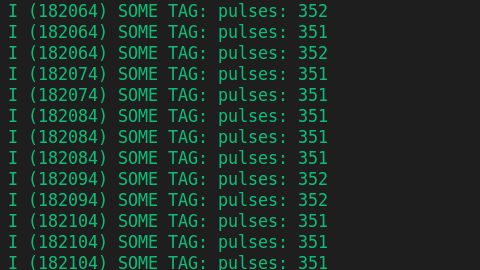
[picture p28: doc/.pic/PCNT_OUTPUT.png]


And the given output is exactly matching our expectations. Yaay!

## 18/04/21

Today I fixed some issues with the dev-diary, and started to learn freeRTOS. A simple task will run on the ESP32 which is to read all three sensors values. For this reason I have created a new project called `AIS_node_v1`, and collected all I2C, PCNT and GPIO codes that I have written.

First test was a complete success, all values a read correctly. Errors might be happening, so our next objective is to detect errors, and filter them out.

## 20/04/21

Today I wrote a simple task to execute the measurement cycle. I have some concepts about the main architecture of the nodes task system.

The ESP32 uses a modified freeRTOS to run user tasks parallel to WiFi management. My concept for now is the following:

- Tasks:
  - main  -> schedules the measurement task, at 10 seconds or when comm task tells it
  - measure  -> executes a measurement cycle
  - comm  -> receives input from serial port and/or WiFi

``` C

static void measureTask (void* vParam){

    uint8_t lm_data[2] = {0,0};
    uint8_t veml_data[2] = {13,15};

    while (1)
    {

        pcnt_counter_clear(PCNT_UNIT_0);
        vTaskDelay(100/portTICK_PERIOD_MS);   
        pcnt_get_counter_value(PCNT_UNIT_0, (int16_t*)&cnt);

        readLM(lm_data, 2);
        temperature = lm_data[0];

        readVEML(veml_data, 2);
        light = (256*veml_data[1]+veml_data[0]);

        // temporary:
        ESP_LOGI(TAG, "measured values %d, %d, %d", temperature, light, cnt);

    }  
}
```
This is the measurement task. `vTaskDelay()` and `vTaskDelayUntil()` functions seems to be equivalent in use in this case.

Default timing will be done with suspended state. Measurement task has been appended with a self suspending function, (`vTaskSuspend(NULL)`) and the main task will, resume the task with `vTaskResume(<tskHandle>)`.

Added mutexes for data variables, and a measurement control boolean variable. A new task has been created, named main. for the 10 second timing, I use a software timer.

For reasons I have not yet found, I am getting continuous chip resets. The problem might be with the mutexes, according to the debug logs.

## 21/04/21

Quick log for today, because I am tired. The improvements and modifications that I made:

  - All `ESP_LOGI` / `ESP_LOGE` macros are deleted, from now on we only use `printf()` which happened to be working for some reason.
  - mutexes are deleted as long as the main project has serious problems with task management
  - watchdogs will remain a problem so they are still turned off in the project
  - `xTaskCreate()` functions are expecting to get handler pointer which caused a metric ton of problems, this is now fixed.
  - unused PCNT counter event values are set to zero, because they were producing errors every startup (doesn't seems to affect the whole progression tho)
  - started an uart project to learn uart configuration, but no need to it, so the project is abandoned for the time being
  - tweaked delay time to 1 sec, for debug purposes
  - increased stack sizes to `2048`, from original `configMINIMAL_STACK_SIZE`
  - `app_main()` task is suspended, after creating the three tasks (`main`, `measure`, `timer`)

## 22/04/21

Today I reworked the task structure. Task `measureTask` task is no longer suspends itself after every iteration, instead it delays itself for a small amount of time. Task `mainTask` is responsible for reading the measured data and calculate an average from every 10 measured value. For easier data management I have created a struct:

``` C
typedef struct {
    uint16_t cnt;
    uint16_t light;
    uint8_t temperature;
}data_pack;

```

This struct contains all measured data that we have to manage.

Inter-task communication is done with a queue (default freeRTOS API). The Queue is 10 long, but it is an overkill, because main can drain all data faster than measure can load.

Mutexes are removed because there is no global variable needs to be accessed simultaneously.

I also created a function to calculate averages (`xAverage`) but it doesn't give accurate results.

## 23/04/21

The average counter function was providing false data because printf() received wrong arguments firs time, and some overflow error happened as well. After that fixed and some small simplification in the average counting function, we are getting correct results.

`mainTask` is renamed to be `processTask` from now on, it represents the tasks purpose better.

Measurements control is restored to the software timer, therefore more precise cycles can be achieved:
  - `measureTask` is now suspends itself (again)
  - timer is resuming it from a callback function

I have looked through the code, and deleted unnecessary segments like mutex declarations, unused global variables etc.

Defines have been created for further readability, and queue length has been decreased to 3, because 10 length queue was an overkill, and 3 is just enough.
To be fair one is enough, because with default configuration, the queue doesn't hold more than one item at any time. 3 is only for security.

## 05/05/21

Finally we have a working and more or less well functional prototype. I have found a program called `screen` which is more comfortable in development to use. with the command : `screen /dev/ttyUSB0 115200` I can easily monitor the serial port while the integrated shell in VSCode remains untouched and more comfortable to work with.
I have also moved credentials to a different header file, this way, the user can change it on its own, before compile, and my credentials are not stored publicly on github.

A bug has also been fixed about the JSON standard (As of yet, I have used single quotes instead of dual ones). Now the transmitted JSON string is correct.

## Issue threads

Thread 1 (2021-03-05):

Protection Diode missing in Capacity screw terminal

GaryBlackbourne, 2021-03-05:
At the moment, the screw terminal is directly connected to 555 timer.
A protection diode is needed, if external use is needed.

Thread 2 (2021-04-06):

PWR diode missing

GaryBlackbourne, 2021-04-06:

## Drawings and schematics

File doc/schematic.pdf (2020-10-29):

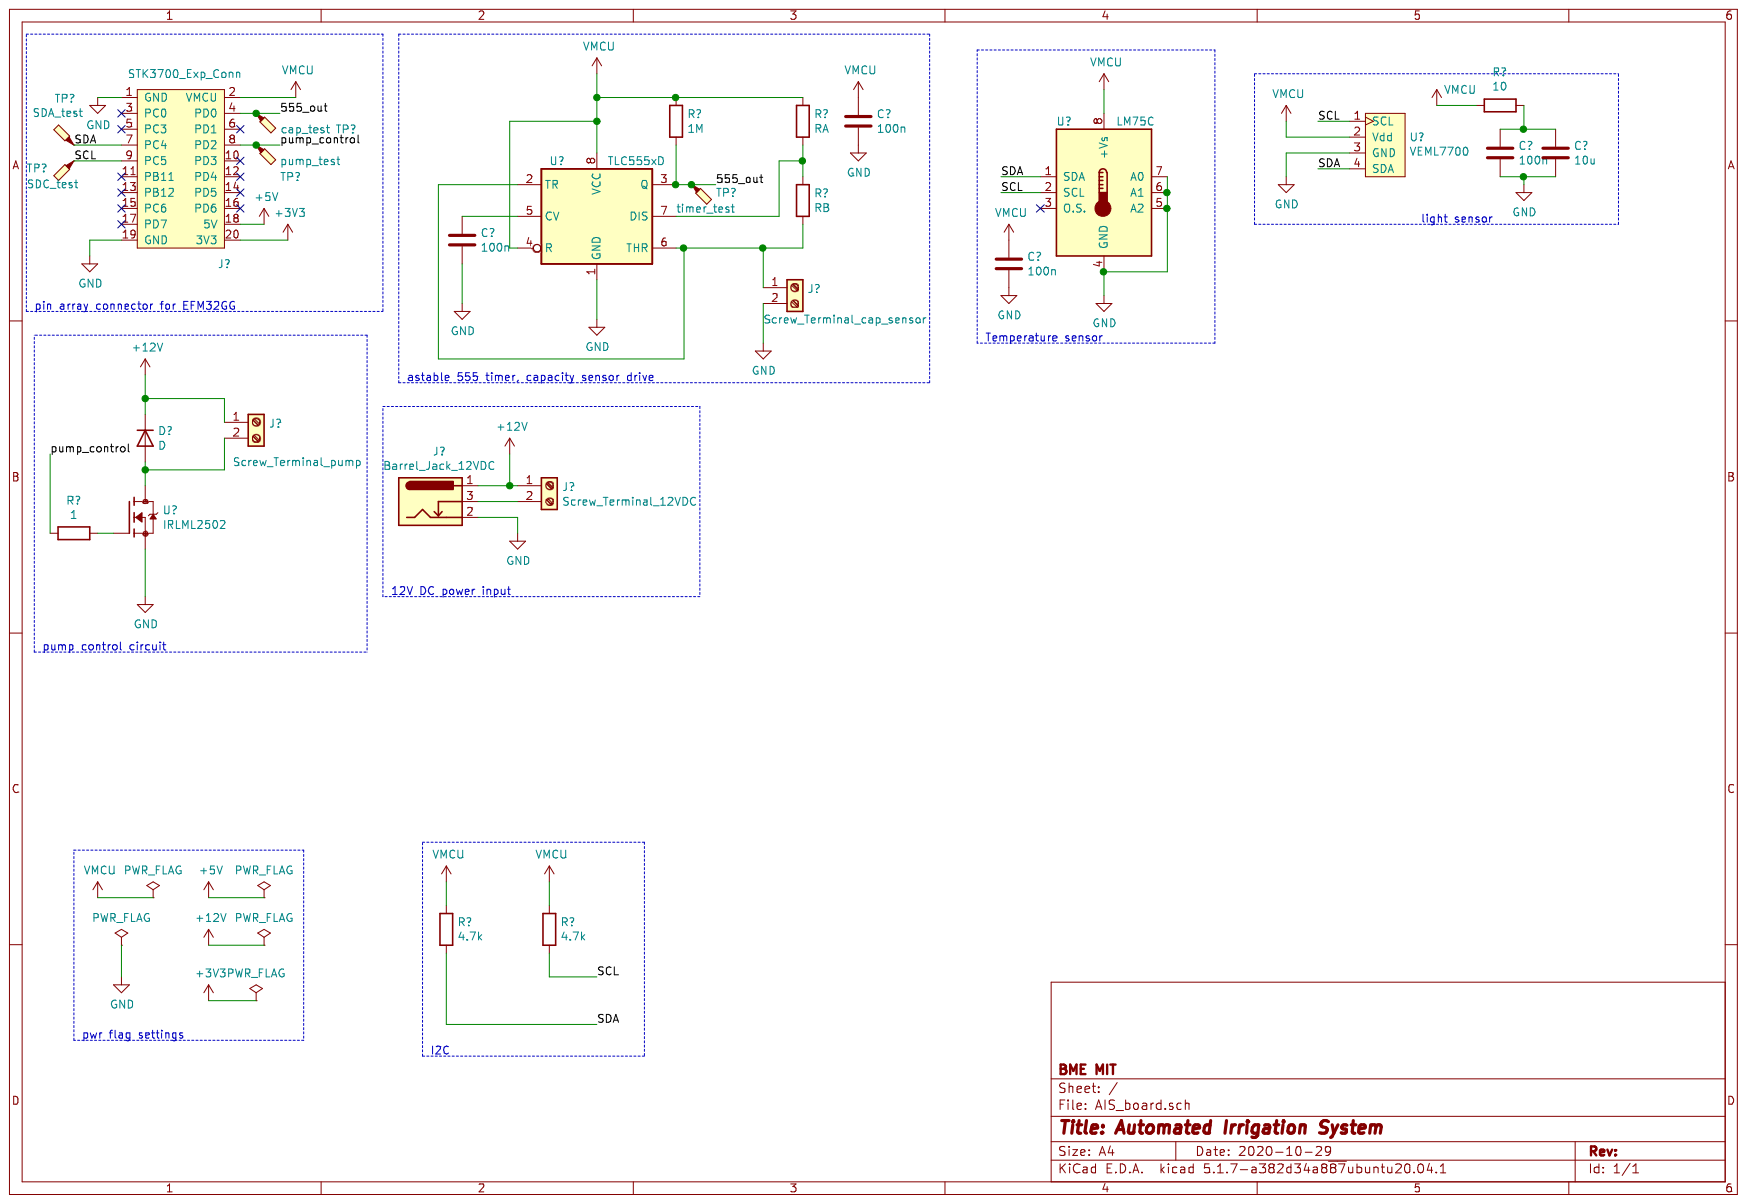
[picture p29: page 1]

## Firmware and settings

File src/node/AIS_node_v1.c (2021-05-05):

#include <stdio.h>

#include "driver/pcnt.h"
#include "driver/i2c.h"
#include "driver/gpio.h"

#include "freertos/FreeRTOS.h"
#include "freertos/semphr.h"
#include "freertos/timers.h"
#include "freertos/task.h"
#include "freertos/event_groups.h"

#include "esp_wifi.h"
#include "esp_http_server.h"
#include "nvs_flash.h"

// ------------------------------------------
// AIS includes
// ------------------------------------------
#include "AIS_config.h"
#include "credentials.h"

// ------------------------------------------
// data struct definition:
// ------------------------------------------

// data struct definition:
typedef struct {
    uint16_t cnt; // temp 32 bit 
    uint16_t light;
    uint8_t temperature;
}data_pack;


// ------------------------------------------
// Global variables:
// ------------------------------------------

// measurements:

uint8_t latestMeasurement = 0;
data_pack measurements [2];

// freeRTOS:

// queue:
static QueueHandle_t data_queue;

// ------------------------------------------
// networking:
// ------------------------------------------

// WiFi:

// handlers and variables:
static EventGroupHandle_t s_wifi_event_group;
static int s_retry_count = 0;

// event handler:
static void event_handler(void* arg, esp_event_base_t event_base, int32_t event_id, void* event_data){
    if(event_base == WIFI_EVENT && event_id == WIFI_EVENT_STA_START){
    
        esp_wifi_connect();
    
    }else if (event_base == WIFI_EVENT && event_id == WIFI_EVENT_STA_DISCONNECTED){
        
        if(s_retry_count < MAX_RETRY_COUNT){
            esp_wifi_connect();
            s_retry_count ++;
            printf("Retry to connect to the AP \n\r");
        }else{
            xEventGroupSetBits(s_wifi_event_group, WIFI_FAIL_BIT);
        }
        printf("Connect to the AP fail \n\r");

    }else if(event_base == IP_EVENT && event_id == IP_EVENT_STA_GOT_IP){
        
        ip_event_got_ip_t* event = (ip_event_got_ip_t*) event_data;
        printf("Got IP: " IPSTR "\n\r", IP2STR(&event->ip_info.ip));
        s_retry_count = 0;
        xEventGroupSetBits(s_wifi_event_group, WIFI_CONNECTED_BIT);
    
    }
}

//init:
void wifi_init_sta(){
    s_wifi_event_group = xEventGroupCreate();

    ESP_ERROR_CHECK(esp_netif_init());
    
    ESP_ERROR_CHECK(esp_event_loop_create_default());
    esp_netif_create_default_wifi_sta();

    wifi_init_config_t cfg = WIFI_INIT_CONFIG_DEFAULT();
    ESP_ERROR_CHECK(esp_wifi_init(&cfg));

    esp_event_handler_instance_t instance_any_id;
    esp_event_handler_instance_t instance_got_ip;

    ESP_ERROR_CHECK(
        esp_event_handler_instance_register(
            WIFI_EVENT,
            ESP_EVENT_ANY_ID,
            &event_handler,
            NULL,
            &instance_any_id
        )
    );

    ESP_ERROR_CHECK(
        esp_event_handler_instance_register(
            IP_EVENT,
            IP_EVENT_STA_GOT_IP,
            &event_handler,
            NULL,
            &instance_got_ip
        )
    );


    wifi_config_t wifi_config = {
        .sta = {
            .ssid = SSID,
            .password = PASSPHRASE,
            
            .threshold.authmode = WIFI_AUTH_WPA2_PSK,
            
            .pmf_cfg = {
                .capable = true,
                .required = false,
            }
        }
    };

    ESP_ERROR_CHECK(esp_wifi_set_mode(WIFI_MODE_STA));
    ESP_ERROR_CHECK(esp_wifi_set_config(WIFI_IF_STA, &wifi_config));
    ESP_ERROR_CHECK(esp_wifi_start());

    printf("Wifi initialization finished. \n\r");

    EventBits_t bits = xEventGroupWaitBits(
        s_wifi_event_group,
        WIFI_CONNECTED_BIT | WIFI_FAIL_BIT,
        pdFALSE,
        pdFALSE,
        portMAX_DELAY
    );

    if(bits & WIFI_CONNECTED_BIT) {
        printf("ESP connected to AP: %s \n\r", SSID);
    }else if(bits & WIFI_FAIL_BIT){
        printf("Failed to connect AP: %s \n\r", SSID);
    }else{
        printf("Unexpected event! \n\r");
    }

    ESP_ERROR_CHECK(esp_event_handler_instance_unregister(IP_EVENT, IP_EVENT_STA_GOT_IP, instance_got_ip));
    ESP_ERROR_CHECK(esp_event_handler_instance_unregister(WIFI_EVENT, ESP_EVENT_ANY_ID, instance_any_id));
    vEventGroupDelete(s_wifi_event_group);
    return;
}

// HTTP:

/* URI handler functions: */
esp_err_t get_handler(httpd_req_t *req){
    const char resp[] = "URI GET Response";
    httpd_resp_send(req, resp, HTTPD_RESP_USE_STRLEN);
    return ESP_OK;
}

esp_err_t post_handler(httpd_req_t *req){
    return ESP_OK;
}

esp_err_t get_default_handler(httpd_req_t *req){
    printf("Someone accessed home! \n\r");
    httpd_resp_send(req, "ESP32 node is online... \n\r", HTTPD_RESP_USE_STRLEN);
    return ESP_OK;
}

esp_err_t get_measure_handler(httpd_req_t *req){
    
    char meas_msg_json[100] = "";
    
    sprintf(meas_msg_json, "{ \"pulses\" : %d, \"light\" : %d, \"temperature\" : %d}\n\r",
                    measurements[latestMeasurement].cnt,
                    measurements[latestMeasurement].light,
                    measurements[latestMeasurement].temperature
                    );
    printf(meas_msg_json);

    httpd_resp_send(req, meas_msg_json, HTTPD_RESP_USE_STRLEN);

    return ESP_OK;
}

/* URI handlers structure for GET/POST /uri */
httpd_uri_t uri_get = {
    .uri      = "/uri",
    .method   = HTTP_GET,
    .handler  = get_handler,
    .user_ctx = NULL
};

httpd_uri_t uri_post = {
    .uri      = "/uri",
    .method   = HTTP_POST,
    .handler  = post_handler,
    .user_ctx = NULL
};

httpd_uri_t uri_get_default = {
    .uri      = "/",
    .method   = HTTP_GET,
    .handler  = get_default_handler,
    .user_ctx = NULL
};

httpd_uri_t uri_get_measure = {
    .uri      = "/measure",
    .method   = HTTP_GET,
    .handler  = get_measure_handler,
    .user_ctx = NULL
};

/* start stop functions */
httpd_handle_t startServer(){
    httpd_config_t server_config = HTTPD_DEFAULT_CONFIG();
    httpd_handle_t server_handle = NULL;

    if(httpd_start(&server_handle, &server_config) == ESP_OK){
        httpd_register_uri_handler(server_handle, &uri_get);
        httpd_register_uri_handler(server_handle, &uri_post);
        httpd_register_uri_handler(server_handle, &uri_get_default);
        httpd_register_uri_handler(server_handle, &uri_get_measure);
    }

    return server_handle;
}

void stopServer(httpd_handle_t server_handle){
    if(server_handle){
        httpd_stop(server_handle);
    }
}

// ------------------------------------------
// init structs:
// ------------------------------------------

// pcnt:
pcnt_config_t pcntInitStruct = {
        .pulse_gpio_num = PCNT_GPIO_NUM_PULSE,
        .ctrl_gpio_num = PCNT_GPIO_NUM_CTRL,
        .lctrl_mode = PCNT_MODE_KEEP,
        .hctrl_mode = PCNT_MODE_KEEP,
        .pos_mode = PCNT_COUNT_INC, 
        .neg_mode = PCNT_COUNT_DIS,
        .counter_h_lim = 0, 
        .counter_l_lim = 0, 
        .unit = PCNT_UNIT_0,
        .channel = PCNT_CHANNEL_0
    };

// i2c:
i2c_config_t init_i2c = {
    
        .mode = I2C_MODE_MASTER,
        
        .sda_io_num = I2C_SDA_PIN,
        .sda_pullup_en = GPIO_PULLUP_ENABLE,
        
        .scl_io_num = I2C_SCL_PIN,
        .scl_pullup_en = GPIO_PULLUP_ENABLE,

        .master.clk_speed = I2C_SCL_FREQ
    };

// gpio:
gpio_config_t init_gpio = {

    .pin_bit_mask = GPIO_SELECTED_PIN_MSK,
    .mode = GPIO_MODE_OUTPUT,
    .intr_type = GPIO_INTR_DISABLE,
    .pull_down_en = GPIO_PULLDOWN_DISABLE,
    .pull_up_en = GPIO_PULLUP_DISABLE,
};

// ------------------------------------------
// init functions:
// ------------------------------------------

// pcnt:
void pcntInit(){

    pcnt_unit_config(&pcntInitStruct);
    pcnt_intr_disable(PCNT_UNIT_0);
    pcnt_counter_clear(PCNT_UNIT_0);
    return;
}

// i2c:
void I2CInit(){
    
    i2c_param_config(I2C_NUM_0, &init_i2c);
    i2c_driver_install(I2C_NUM_0, init_i2c.mode, I2C_MASTER_RX_BUF_DISABLE, I2C_MASTER_TX_BUF_DISABLE, 0);   
    return;
}

// veml7700:
void VEMLInit(){

    uint8_t init_command[3] = {0,0,0};

    i2c_cmd_handle_t cmd = i2c_cmd_link_create();

    i2c_master_start(cmd);

    i2c_master_write_byte(cmd, (VEML_ADDR | I2C_MASTER_WRITE), true);

    i2c_master_write(cmd, init_command, 3, true);

    i2c_master_stop(cmd);

    i2c_master_cmd_begin(I2C_NUM_0, cmd, 1000 / portTICK_PERIOD_MS);

    i2c_cmd_link_delete(cmd);

    return;
}

// gpio (pump):
void gpioInit(){
    gpio_config(&init_gpio);
    return;
}

// ------------------------------------------
// sensor read functions:
// ------------------------------------------

// veml7700
void readVEML (uint8_t* data, uint8_t size){

    i2c_cmd_handle_t cmd = i2c_cmd_link_create();

    i2c_master_start(cmd);
    i2c_master_write_byte(cmd, (VEML_ADDR | I2C_MASTER_WRITE), true);
    i2c_master_write_byte(cmd, VEML_COMMAND, true);

    i2c_master_start(cmd);
    i2c_master_write_byte(cmd, (VEML_ADDR | I2C_MASTER_READ), true);
    i2c_master_read(cmd, data, 1, I2C_MASTER_ACK);
    i2c_master_read_byte(cmd, data+1, I2C_MASTER_NACK);
    
    i2c_master_stop(cmd);

    // esp_err_t error2 = i2c_master_cmd_begin(I2C_NUM_0, cmd, 1000 / portTICK_RATE_MS);
    i2c_master_cmd_begin(I2C_NUM_0, cmd, 1000 / portTICK_RATE_MS);
    i2c_cmd_link_delete(cmd);

    return;
}

// lm-75
void readLM (uint8_t* data, uint8_t size){

    i2c_cmd_handle_t cmd = i2c_cmd_link_create();

    i2c_master_start(cmd);

    i2c_master_write_byte(cmd, (LM75_ADDR | I2C_MASTER_READ), true);

    i2c_master_read(cmd, data, size, I2C_MASTER_ACK);

    i2c_master_stop(cmd);

    i2c_master_cmd_begin(I2C_NUM_0, cmd, 1000 / portTICK_RATE_MS);

    i2c_cmd_link_delete(cmd);

    return;
}

// ------------------------------------------
// processing functions:
// ------------------------------------------

data_pack xAverage(data_pack* input, uint8_t size){
    
    data_pack result;
    
    uint32_t cnt = 0;
    uint32_t light = 0;
    uint32_t temperature = 0;

    for(uint8_t i = 0; i < size; i ++){
        cnt += input[i].cnt;
        light += input[i].light;
        temperature += input[i].temperature;
    }
    
    // rounds are small enough
    result.cnt = cnt / size;
    result.light = light / size;
    result.temperature = temperature / size;

    return result;
}

// ------------------------------------------
// Tasks:
// ------------------------------------------

// executes a measurement cycle
TaskHandle_t measureTaskHandle;
static void measureTask (void* vParam){
    
    uint8_t lm_data[2] = {0,0};
    uint8_t veml_data[2] = {0,0};
    uint16_t pCounter = 0;
    data_pack data;

    printf("measure scheduled \n\r"); 

    while (1)
    {
        
        pcnt_counter_clear(PCNT_UNIT_0);
        vTaskDelay(100/portTICK_PERIOD_MS);                         // 100 ms
        pcnt_get_counter_value(PCNT_UNIT_0, (int16_t*)&pCounter);
        
        readLM(lm_data, 2);
        readVEML(veml_data, 2);

        // -------------------------------------
        data.cnt = pCounter;
        data.temperature = lm_data[0];
        data.light = (256*veml_data[1]+veml_data[0]);
        // -------------------------------------

        // temporary:
        // printf("measured values %d, %d, %d \n\r", temperature, light, cnt);
        if(xQueueSend(data_queue, &data, 0) != pdTRUE){
            printf("Failed to wrtie data queue! Queue is full ... \r\n");
        }

        // vTaskDelay(meas_TIME_MS/portTICK_PERIOD_MS);
        vTaskSuspend(NULL); // suspend itself
    }  
}

// SW timer callback function
static void resumeMeasure(){
    
    xTaskResumeFromISR(measureTaskHandle);

    return;
}

// schedules the measurement tasks
TaskHandle_t processTaskHandle;
static void processTask(void* vParam){

    data_pack final_data;

    uint8_t idx = 0;
    data_pack raw_data_array[10];
    printf("process scheduled \n\r");

    while(1){
        if(idx > (meas_LENGTH-1)){ 
            
            idx = 0;
            
            final_data = xAverage(raw_data_array, meas_LENGTH);

            if(latestMeasurement){
                measurements[0] = final_data;
                latestMeasurement = 0;
            }else{
                measurements[1] = final_data;
                latestMeasurement = 1;
            }
            
        }else{
            // read from queue
            if(xQueueReceive(data_queue, (void*)&(raw_data_array[idx]), 0) == pdTRUE){
                idx++;
            }
            // if cant receive, queue is empty
            vTaskDelay(process_DELAY_MS/portTICK_PERIOD_MS);
        }
    }
}

void app_main(void)
{
    esp_err_t ret = nvs_flash_init();
    if (ret == ESP_ERR_NVS_NO_FREE_PAGES || ret == ESP_ERR_NVS_NEW_VERSION_FOUND) {
      ESP_ERROR_CHECK(nvs_flash_erase());
      ret = nvs_flash_init();
    }
    ESP_ERROR_CHECK(ret);

    printf("ESP WiFi mode station \n\r");
    wifi_init_sta();

    startServer();

    gpioInit();
    pcntInit();
    I2CInit();
    VEMLInit();

    data_queue = xQueueCreate(queue_LENGTH, queue_LENGTH*sizeof(data_pack));

    TimerHandle_t measure_timer = xTimerCreate(
                                        "measure scheduler timer",
                                        pdMS_TO_TICKS(meas_TIME_MS),
                                        pdTRUE,
                                        (void*)0,
                                        resumeMeasure
                                    );

    if(measure_timer == NULL){
        printf("Timer initialization failed \n\r");
    }else{
        vTaskDelay(1000/portTICK_PERIOD_MS);
        
        xTimerStart(measure_timer, portMAX_DELAY);

        printf("Timer Initialized! \r\n");
    }


    xTaskCreate(
        processTask,                       // tsk function
        "process task",                    // task name 
        2048,                              // stack size
        NULL,                              // parameter list
        processTsk_PRIORITY,               // priority
        &processTaskHandle                 // task handle address
    );


    xTaskCreate(
        measureTask,                    // tsk function
        "measure task",                 // task name 
        2048,                           // stack size
        NULL,                           // parameter list
        measureTsk_PRIORITY,            // priority
        &measureTaskHandle              // task handle address
    );
    
    
    
    // scheduler already running. 

    // suspend own task.
    vTaskSuspend(NULL);
    
}

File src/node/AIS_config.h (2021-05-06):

#ifndef AIS_CONFIG_H
#define AIS_CONFIG_H

#include "credentials.h"

// ------------------------------------------
// defines:
// ------------------------------------------


#define I2C_MASTER_RX_BUF_DISABLE 0
#define I2C_MASTER_TX_BUF_DISABLE 0
#define I2C_SDA_PIN GPIO_NUM_18
#define I2C_SCL_PIN GPIO_NUM_19
#define I2C_SCL_FREQ 20000                              // 20kHz signal

#define LM75_ADDR (uint8_t)0x90
#define VEML_ADDR (uint8_t)0x20
#define VEML_COMMAND (uint8_t)0x04

#define GPIO_SELECTED_PIN GPIO_NUM_2                    // = 2
#define GPIO_SELECTED_PIN_MSK (1ULL << GPIO_SELECTED_PIN)

#define PCNT_GPIO_NUM_CTRL GPIO_NUM_23
#define PCNT_GPIO_NUM_PULSE GPIO_NUM_22


#define measureTsk_PRIORITY (tskIDLE_PRIORITY + 2)
#define processTsk_PRIORITY (tskIDLE_PRIORITY + 1)

#define meas_TIME_MS 10000                          // 0,5 sec
#define process_DELAY_MS 10                         // data processing tasks delay value in miliseconds
#define meas_LENGTH 10                              // the amount of measurements one cycle contains (average will be the measured value)
#define queue_LENGTH  3                             


#define WIFI_CONNECTED_BIT BIT0
#define WIFI_FAIL_BIT      BIT1
#define MAX_RETRY_COUNT 30




#endif

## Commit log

2020-10-20 Created kiCAD project
    [AIS_board.kicad_pcb, AIS_board.sch]
2020-10-27 Added symbol library to the project, designed basic connection to EFM32GG
    [AIS_board.sch]
2020-10-27 Created astable timer from TLC555 IC
    [AIS_board.sch]
2020-10-28 Added LM75C temperature sensor chip
    [AIS_board.sch]
2020-10-28 Added LM7700 light sensor chip
    [AIS_board.sch]
2020-10-28 Added pdf for schematic preview. (removed git test from NOTES.txt)
2020-10-28 Redrawn 555 astable timer schematic, to mach datasheet circuit
    [AIS_board.sch]
2020-10-28 Added IP65 protective case to documentation
2020-10-28 Added water pump to the project documentation
2020-10-28 Added common source circuit, to drive the pump
    [AIS_board.sch]
2020-10-29 Added 555 timer out resistor, RL
    [AIS_board.sch]
2020-10-29 Added power supply module to the documentation
2020-10-29 Added connectors to the schematic, designed capacity sensor head module and power in
    [AIS_board.sch]
2020-10-29 Added comments for schematic, and added documentation for screw terminals
    [AIS_board.sch]
2020-10-29 Updated schematic pdf
2020-10-29 Added .gitignore for kicad
2020-10-29 Added pwr flags, and I2C pwr resistors to circuit
    [AIS_board.sch]
2020-10-29 Added capacitors to IC power stabilization
    [AIS_board.sch]
2020-10-29 Updated schematic pdf in doc
2020-10-29 Added datasheet for efm32gg microcontroller; added GPIO to pump control, and cap. sensor
    [AIS_board.sch]
2020-10-29 Updated schematic.pdf
2020-10-29 Added test points to schematic
    [AIS_board.sch]
2020-10-29 Corrected RC at VEML7700 PWR input
    [AIS_board.sch]
2020-10-29 Added security 3pin barrel jack, for pwr in
    [AIS_board.sch]
2020-10-29 Added .usrbckp for .gitignore, added numeric values to components
    [AIS_board.sch]
2020-10-29 Redesigned capacitance sensor, removed head module, updated schematic.pdf
    [AIS_board.sch]
2020-10-29 Updated documentation, renamed 555 timer circuit in schematic
    [AIS_board.sch]
2020-10-30 Added annotation to schematic, removed unnecessary test pin
    [AIS_board.sch]
2020-10-30 Added footprint libraries to project, created footprint assignment
    [AIS_board.sch]
2020-10-30 Initial board setup imported
2020-10-30 Fixed VEML7700 power supply in schematic
    [AIS_board.kicad_pcb, AIS_board.sch]
2020-10-30 Refreshed netlist and pcb
    [AIS_board.kicad_pcb]
2020-10-30 Created pcb layout, finished routing
    [AIS_board.kicad_pcb]
2020-10-30 Added GND zone, and pcb silkscreen help text
    [AIS_board.kicad_pcb, AIS_board.sch]
2020-10-30 Fixed not connected GND junction
    [AIS_board.kicad_pcb]
2020-10-31 Removed GND filled zones (plan for VMCU zone), resized traces, fixed routing
    [AIS_board.kicad_pcb]
2020-10-31 Restored GND filled zones to board, fixed minor mispacements
    [AIS_board.kicad_pcb]
2020-10-31 Changed footprints for Capacitors (0603), and barrel jack
    [AIS_board.kicad_pcb, AIS_board.sch]
2020-10-31 Added connection to new barrel jack footprint
    [AIS_board.kicad_pcb]
2020-10-31 Added filled zones
    [AIS_board.kicad_pcb]
2020-10-31 Added filled zones, and diode to parts list
    [AIS_board.kicad_pcb]
2020-10-31 Fixed silkscreen issues, added date, designer name, and board version
    [AIS_board.kicad_pcb]
